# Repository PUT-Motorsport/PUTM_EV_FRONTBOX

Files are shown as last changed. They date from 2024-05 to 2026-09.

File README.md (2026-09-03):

# PUTM_EV_Frontbox

PCB board aquiring data from the front side of the vehicle.

# Features

- APPS
  - read position of acceleration pedal and send to VCU
  - two outputs: power (+5V) lines with separate regulators
  - two inputs: APPS signal lines
  - check plasubility between two signal lines
- Data acquisition
  - front and rear brake pressure measurement
  - safety sensing
  - brake pedal position sensor for regenerative braking

### APPS

- 2 linear potentiometers mounted on pedal
- hardware filter and voltage clamp
- 2 diffrent transfer function to detect implasubility when defect occurs

### Front and rear brake pressure

- two analog, 5V sensors
- hardware filter and voltage clamp

### Safety (shutdown circuit) sensing
Optocupler to check state of SDC curcuit, shift level from 24V to 3V3 and read on MCU digital input
The safety state will be measured at:
- left kill switch
- right kill switch
- driver's kill switch
- inertia switch
- BSPD
- brake overtravel
- suspension interlocks

### Brake pedal position sensor
TBD

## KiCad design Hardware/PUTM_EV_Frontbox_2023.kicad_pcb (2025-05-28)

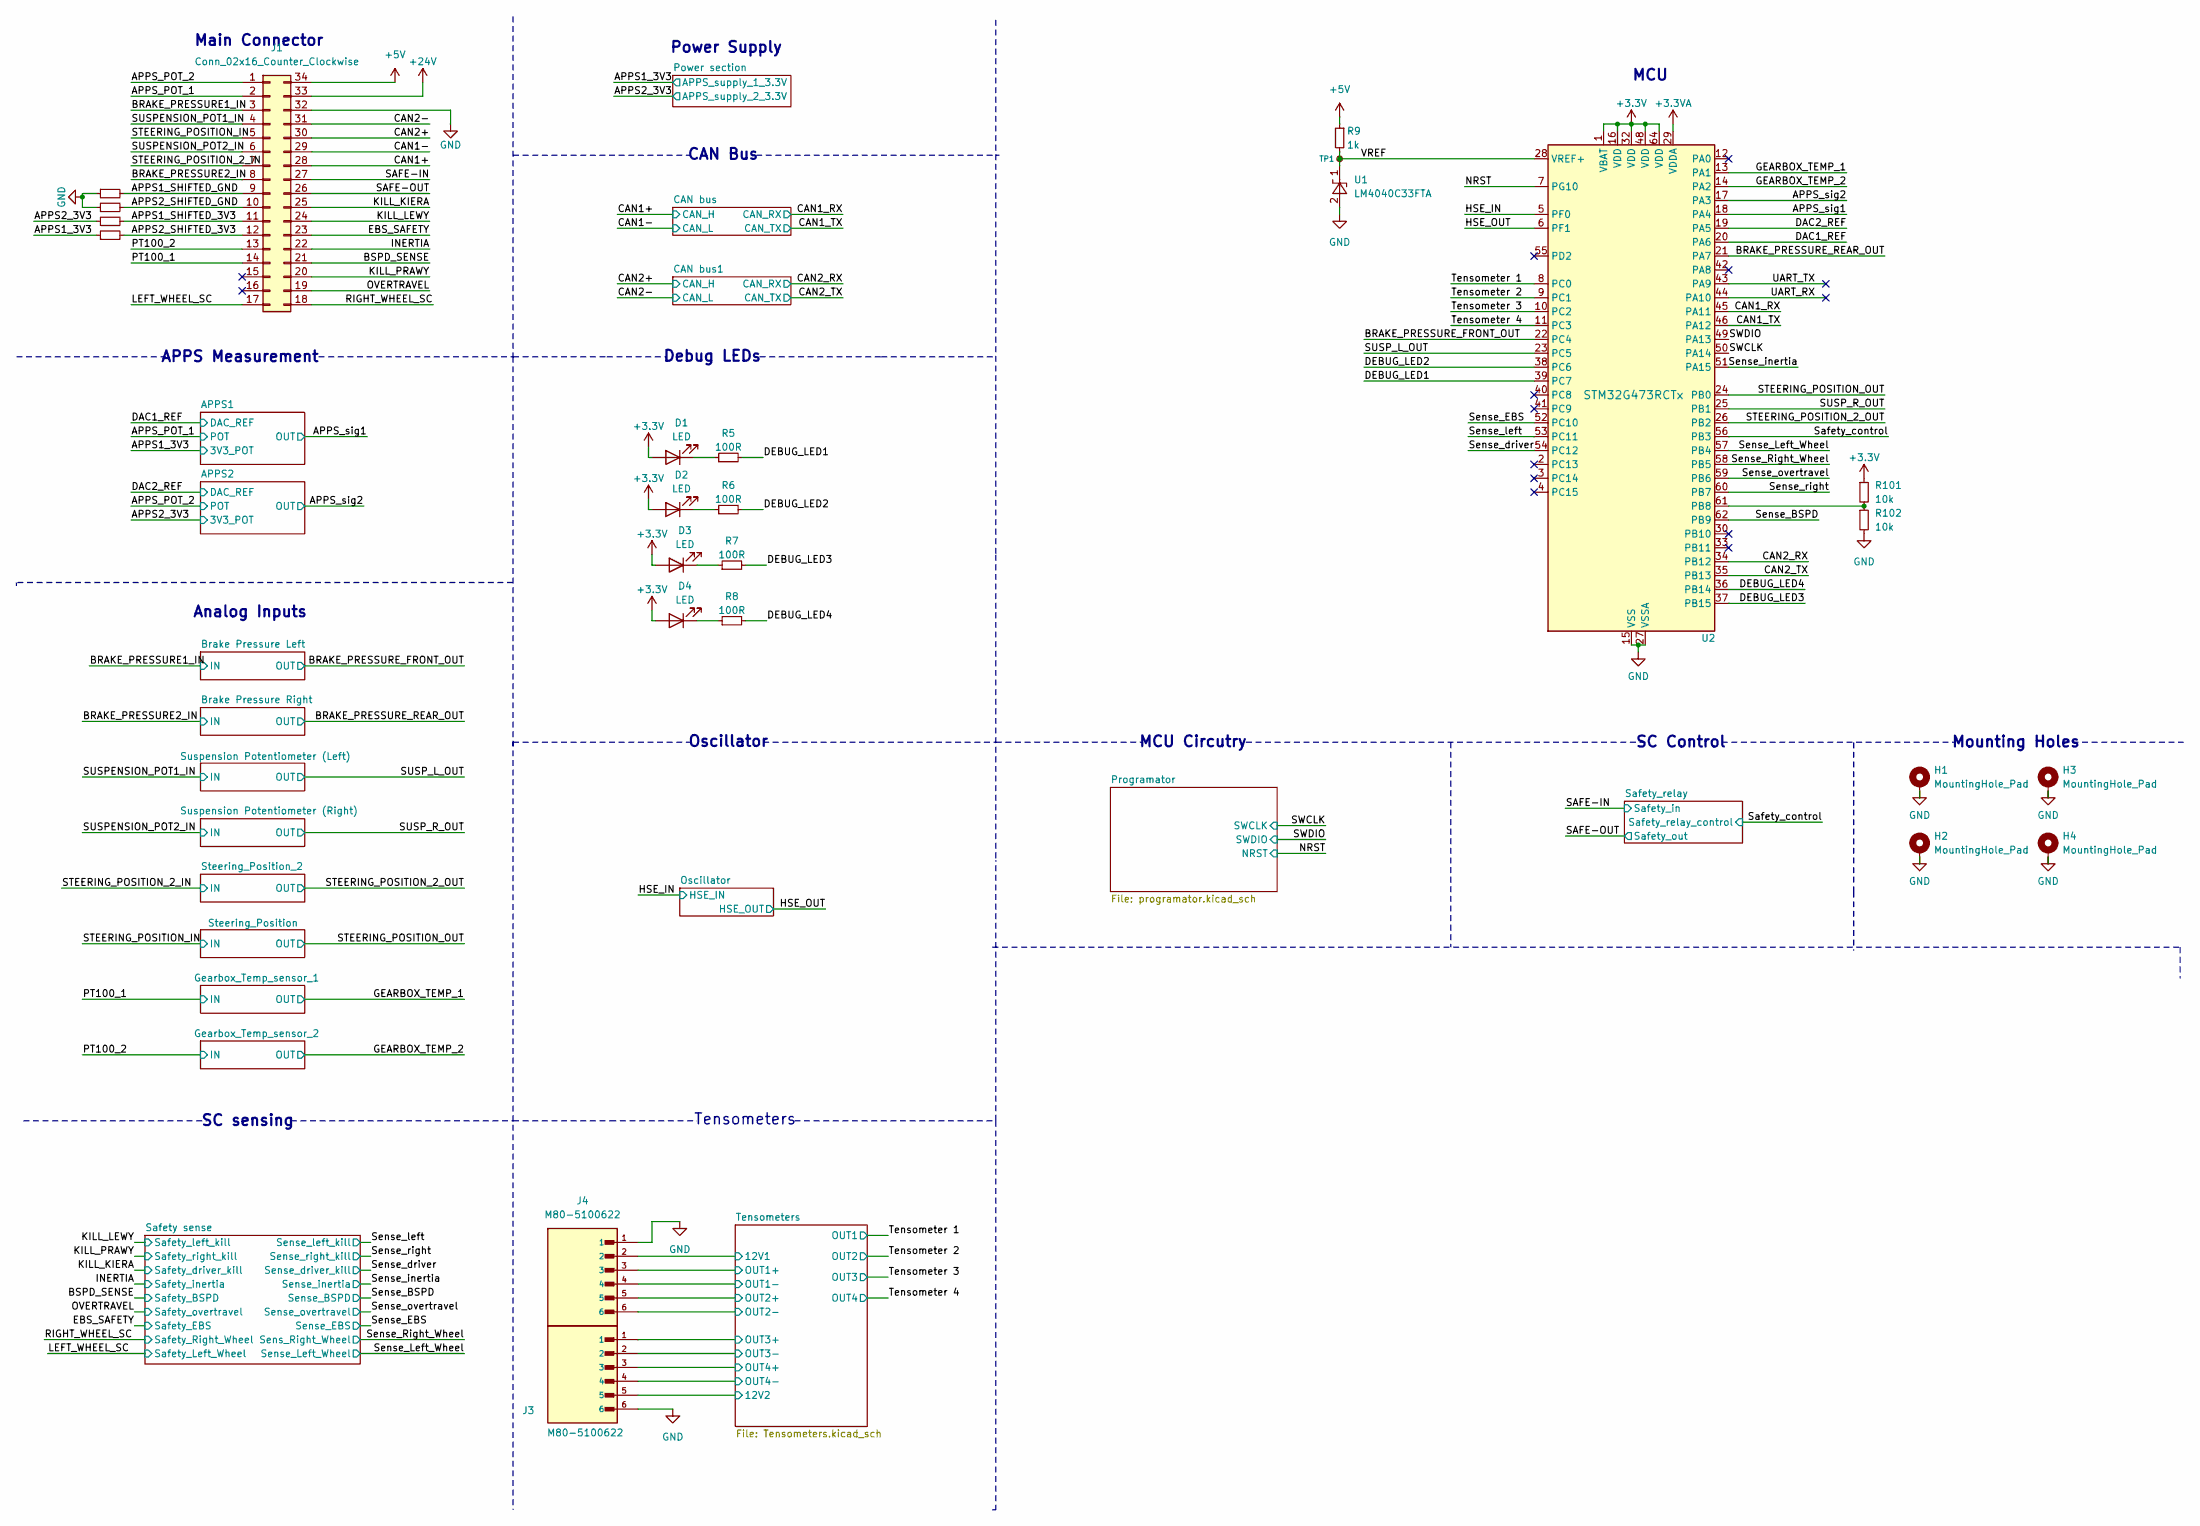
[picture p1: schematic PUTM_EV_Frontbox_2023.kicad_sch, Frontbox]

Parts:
D1, D2, D3, D4: LED; LED_0603_1608Metric_Pad1.05x0.95mm_HandSolder
H1, H2, H3, H4: MountingHole_Pad; MountingHole_3.2mm_M3_Pad_Via
J1: Conn_02x16_Counter_Clockwise; IDC-Header_2x17-1MP_P2.54mm_Latch6.5mm_Vertical
J3, J4: M80-5100622; M80-5100622_HARWIN_M80-5100622
R1, R2, R3, R4: 220R; R_0603_1608Metric_Pad0.98x0.95mm_HandSolder
R5, R6, R7, R8: 100R; R_0603_1608Metric_Pad0.98x0.95mm_HandSolder
R9: 1k; R_0603_1608Metric
R101, R102: 10k; R_0603_1608Metric
TP1: TestPoint_Small; TestPoint_THTPad_D1.0mm_Drill0.5mm
U1: LM4040C33FTA; SOT-23
U2: STM32G473RCTx; LQFP-64_10x10mm_P0.5mm

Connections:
+3.3V: D1.2 (A), D2.2 (A), D3.2 (A), D4.2 (A), R101.1, U2.1 (VBAT), U2.16 (VDD), U2.32 (VDD), U2.48 (VDD), U2.64 (VDD); also elsewhere on the board
+5V: J1.34, R9.1; also elsewhere on the board
+24V: J1.33; also elsewhere on the board
/APPS1_3V3: R4.1; also elsewhere on the board
/APPS1_SHIFTED_3V3: J1.11, R3.2
/APPS1_SHIFTED_GND: J1.9, R1.2
/APPS2_3V3: R3.1; also elsewhere on the board
/APPS2_SHIFTED_3V3: J1.12, R4.2
/APPS2_SHIFTED_GND: J1.10, R2.2
/APPS_POT_1: J1.2; also elsewhere on the board
/APPS_POT_2: J1.1; also elsewhere on the board
/BRAKE_PRESSURE1_IN: J1.3; also elsewhere on the board
/BRAKE_PRESSURE2_IN: J1.8; also elsewhere on the board
/BSPD_SENSE: J1.21; also elsewhere on the board
/CAN1+: J1.28; also elsewhere on the board
/CAN1-: J1.29; also elsewhere on the board
/CAN2+: J1.30; also elsewhere on the board
/CAN2-: J1.31; also elsewhere on the board
/DEBUG_LED1: R5.2, U2.39 (PC7); also elsewhere on the board
/DEBUG_LED2: R6.2, U2.38 (PC6); also elsewhere on the board
/DEBUG_LED3: R7.2, U2.37 (PB15); also elsewhere on the board
/DEBUG_LED4: R8.2, U2.36 (PB14); also elsewhere on the board
/EBS_SAFETY: J1.23; also elsewhere on the board
/INERTIA: J1.22; also elsewhere on the board
/KILL_KIERA: J1.25; also elsewhere on the board
/KILL_LEWY: J1.24; also elsewhere on the board
/KILL_PRAWY: J1.20; also elsewhere on the board
/LEFT_WHEEL_SC: J1.17; also elsewhere on the board
/OVERTRAVEL: J1.19; also elsewhere on the board
/PT100_1: J1.14; also elsewhere on the board
/PT100_2: J1.13; also elsewhere on the board
/RIGHT_WHEEL_SC: J1.18; also elsewhere on the board
/SAFE-IN: J1.27; also elsewhere on the board
/SAFE-OUT: J1.26; also elsewhere on the board
/STEERING_POSITION_2_IN: J1.7; also elsewhere on the board
/STEERING_POSITION_IN: J1.5; also elsewhere on the board
/SUSPENSION_POT1_IN: J1.4; also elsewhere on the board
/SUSPENSION_POT2_IN: J1.6; also elsewhere on the board
/Tensometers/12V1: J4.2; also elsewhere on the board
/Tensometers/12V2: J3.5; also elsewhere on the board
/Tensometers/OUT1+: J4.3; also elsewhere on the board
/Tensometers/OUT1-: J4.4; also elsewhere on the board
/Tensometers/OUT2+: J4.5; also elsewhere on the board
/Tensometers/OUT2-: J4.6; also elsewhere on the board
/Tensometers/OUT3+: J3.1; also elsewhere on the board
/Tensometers/OUT3-: J3.2; also elsewhere on the board
/Tensometers/OUT4+: J3.3; also elsewhere on the board
/Tensometers/OUT4-: J3.4; also elsewhere on the board
/VREF: R9.2, TP1.1, U1.1 (K), U2.28 (VREF+); also elsewhere on the board
GND: H1.1, H2.1, H3.1, H4.1, J1.32, J3.6, J4.1, R1.1, R2.1, R102.2, U1.2 (A), U2.15 (VSS), U2.27 (VSSA), U2.31 (VSS), U2.47 (VSS), U2.63 (VSS); also elsewhere on the board
unnamed: D1.1 (K), R5.1
unnamed: D2.1 (K), R6.1
unnamed: D3.1 (K), R7.1
unnamed: D4.1 (K), R8.1
unnamed 173: R101.2, R102.1, U2.61 (PB8); also elsewhere on the board

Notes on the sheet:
SC sensing
MCU Circutry
CAN Bus
Debug LEDs
Analog Inputs
Oscillator
Main Connector
Tensometers
MCU
SC Control
APPS Measurement
Power Supply
Mounting Holes

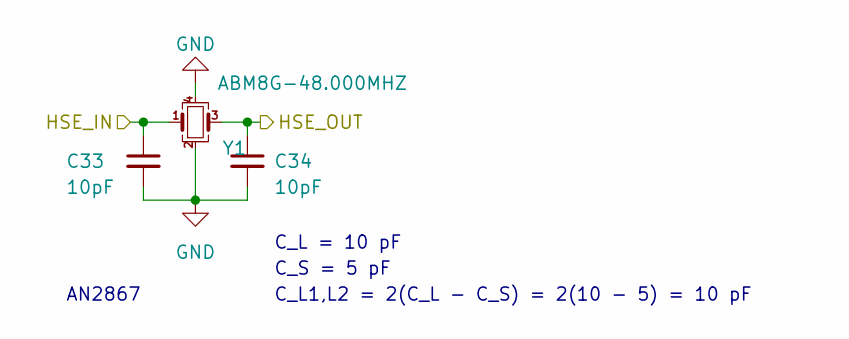
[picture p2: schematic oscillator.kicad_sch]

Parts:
C33, C34: 10pF; C_0402_1005Metric_Pad0.74x0.62mm_HandSolder
Y1: ABM8G-48.000MHZ; Crystal_SMD_Abracon_ABM8G-4Pin_3.2x2.5mm

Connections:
/HSE_IN: C33.1, Y1.1; also elsewhere on the board
/HSE_OUT: C34.1, Y1.3; also elsewhere on the board
GND: C33.2, C34.2, Y1.2, Y1.4; also elsewhere on the board

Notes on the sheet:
C_L = 10 pF
C_S = 5 pF
C_L1,L2 = 2(C_L - C_S) = 2(10 - 5) = 10 pF
AN2867

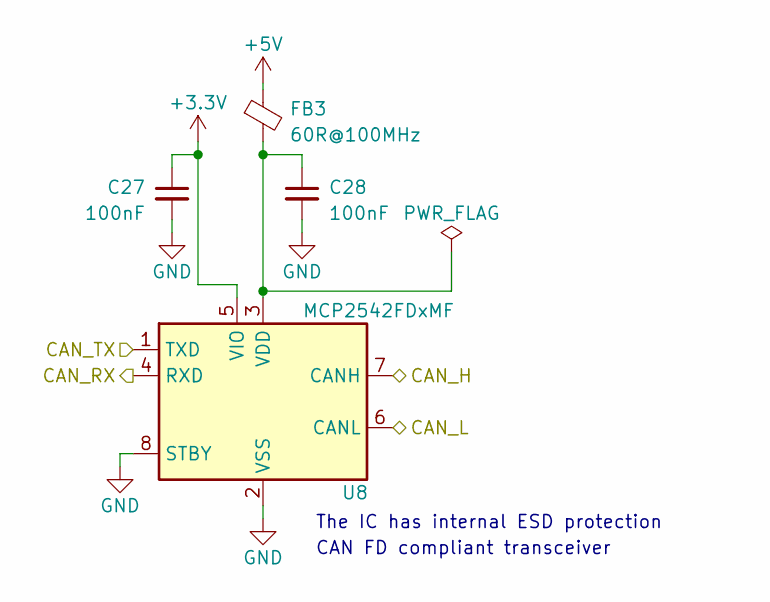
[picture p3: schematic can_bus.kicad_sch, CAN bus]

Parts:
C27, C28: 100nF; C_0402_1005Metric_Pad0.74x0.62mm_HandSolder
FB3: 60R@100MHz; L_0603_1608Metric
U8: MCP2542FDxMF; DFN-8-1EP_3x3mm_P0.65mm_EP1.55x2.4mm

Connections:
+3.3V: C27.1, U8.5 (VIO); also elsewhere on the board
+5V: FB3.1; also elsewhere on the board
/CAN1+: U8.7 (CANH); also elsewhere on the board
/CAN1-: U8.6 (CANL); also elsewhere on the board
/CAN1_RX: U8.4 (RXD); also elsewhere on the board
/CAN1_TX: U8.1 (TXD); also elsewhere on the board
GND: C27.2, C28.2, U8.2 (VSS), U8.8 (STBY), U8.9 (VSS); also elsewhere on the board
unnamed: C28.1, FB3.2, U8.3 (VDD)

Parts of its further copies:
C35, C36: 100nF; C_0402_1005Metric_Pad0.74x0.62mm_HandSolder
FB4: 60R@100MHz; L_0603_1608Metric
U14: MCP2542FDxMF; DFN-8-1EP_3x3mm_P0.65mm_EP1.55x2.4mm

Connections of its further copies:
+3.3V: C35.1, U14.5 (VIO); also elsewhere on the board
+5V: FB4.1; also elsewhere on the board
/CAN2+: U14.7 (CANH); also elsewhere on the board
/CAN2-: U14.6 (CANL); also elsewhere on the board
/CAN2_RX: U14.4 (RXD); also elsewhere on the board
/CAN2_TX: U14.1 (TXD); also elsewhere on the board
GND: C35.2, C36.2, U14.2 (VSS), U14.8 (STBY), U14.9 (VSS); also elsewhere on the board
unnamed: C36.1, FB4.2, U14.3 (VDD)

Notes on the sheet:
The IC has internal ESD protection
CAN FD compliant transceiver

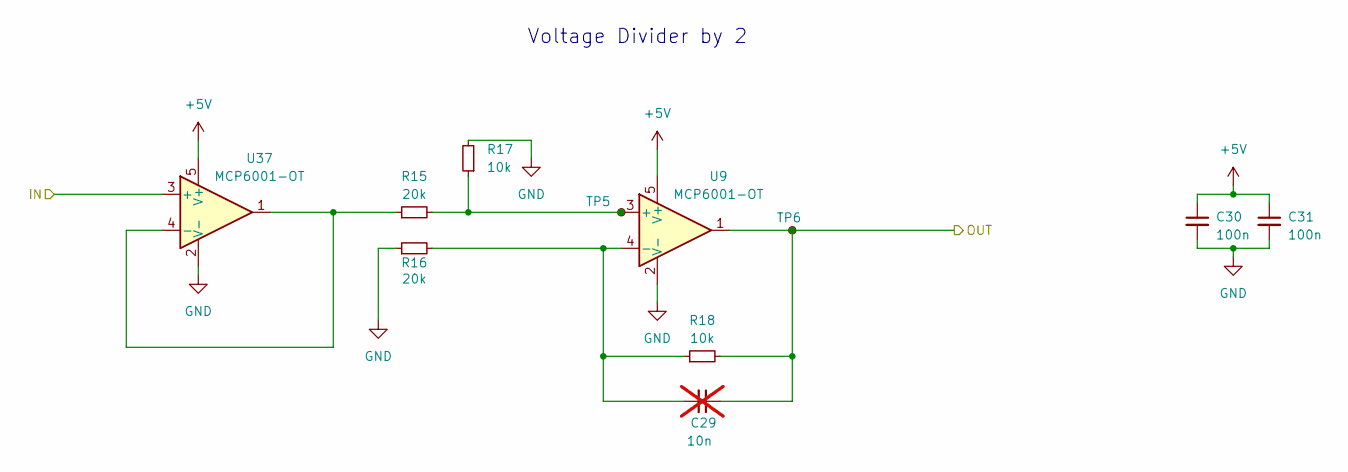
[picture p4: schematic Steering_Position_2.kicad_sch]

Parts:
C29: 10n; C_0603_1608Metric; not fitted
C30, C31: 100n; C_0603_1608Metric
R15, R16: 20k; R_0603_1608Metric
R17, R18: 10k; R_0603_1608Metric
TP5, TP6: TestPoint_Small; TestPoint_THTPad_D1.0mm_Drill0.5mm
U9, U37: MCP6001-OT; SOT-23-5

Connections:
+5V: C30.1, C31.1, U9.5 (V+), U37.5 (V+); also elsewhere on the board
/STEERING_POSITION_2_IN: U37.3 (+); also elsewhere on the board
/STEERING_POSITION_2_OUT: C29.1, R18.2, TP6.1, U9.1; also elsewhere on the board
GND: C30.2, C31.2, R16.1, R17.2, U9.2 (V-), U37.2 (V-); also elsewhere on the board
unnamed: R15.2, R17.1, TP5.1, U9.3 (+)
unnamed: C29.2, R16.2, R18.1, U9.4 (-)
unnamed: R15.1, U37.1, U37.4 (-)

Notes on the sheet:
Voltage Divider by 2

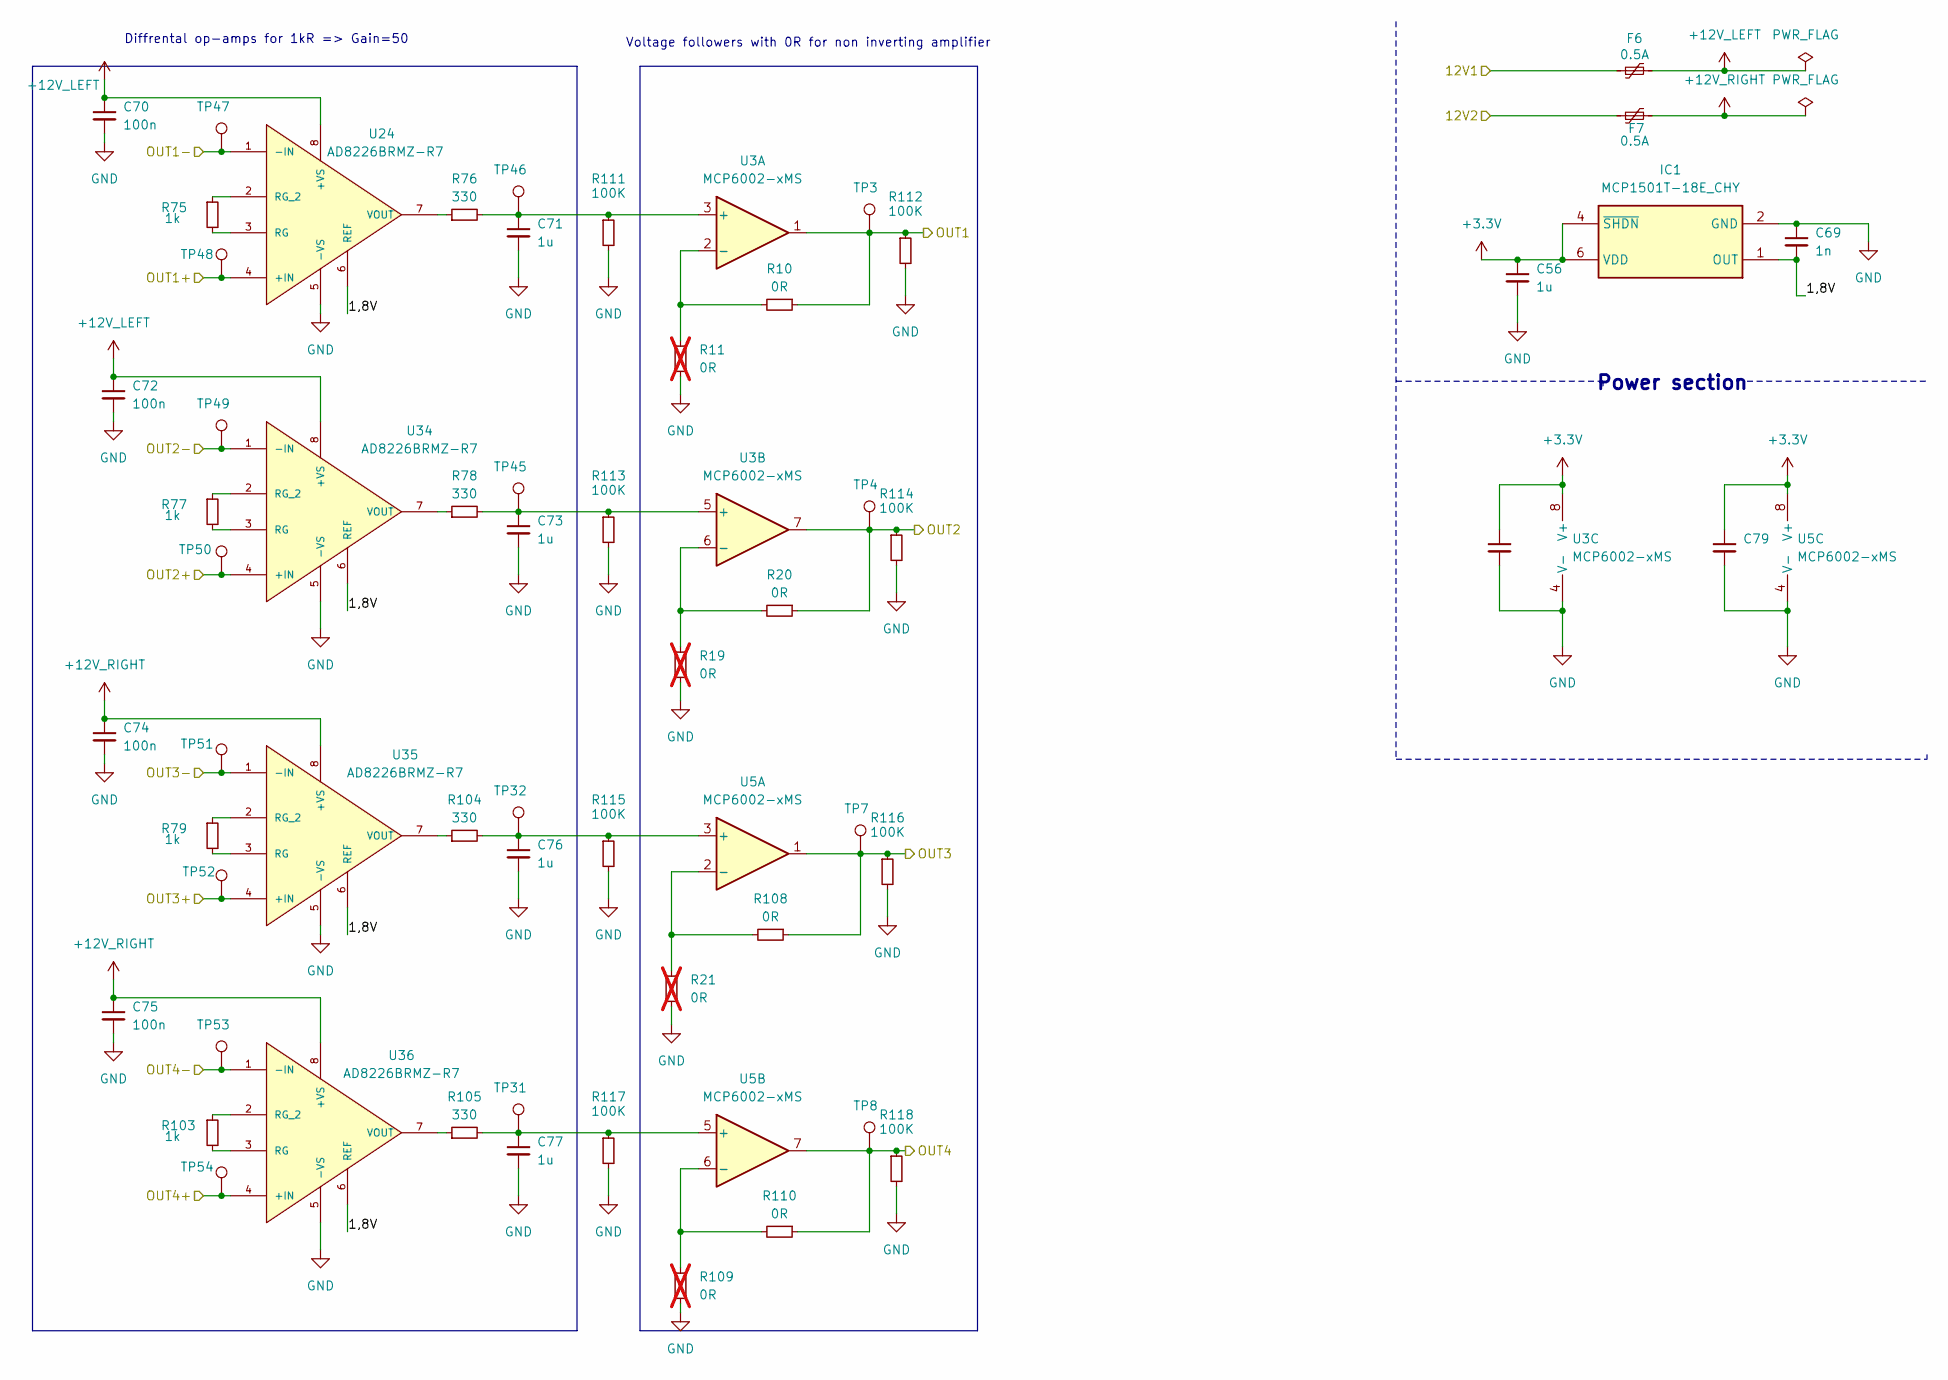
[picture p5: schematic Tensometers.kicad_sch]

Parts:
C56, C71, C73, C76, C77: 1u; C_0603_1608Metric
C69: 1n; C_0603_1608Metric
C70, C72, C74, C75, C78, C79: 100n; C_0603_1608Metric
F6, F7: 0.5A; Fuse_0805_2012Metric
IC1: MCP1501T-18E_CHY; SOT95P270X145-6N; Manufacturer_Part_Number MCP1501T-18E/CHY; Mouser Part Number 579-MCP1501T-18E/CHY
R10, R20, R108, R110: 0R; R_0603_1608Metric
R11, R19, R21, R109: 0R; R_0603_1608Metric; not fitted
R75, R77, R79, R103: 1k; R_0603_1608Metric
R76, R78, R104, R105: 330; R_0603_1608Metric
R111, R112, R113, R114, R115, R116, R117, R118: 100K; R_0603_1608Metric
TP3, TP4, TP7, TP8, TP31, TP32, TP45, TP46, TP47, TP48, TP49, TP50, TP51, TP52, TP53, TP54: BR_N; TestPoint_THTPad_D1.0mm_Drill0.5mm
U3, U5: MCP6002-xMS; SOP65P490X110-8N
U24, U34, U35, U36: AD8226BRMZ-R7; AD8226BRMZ-R7_SOP65P490X110-8N; MPN AD8226BRMZ-R7

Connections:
+3.3V: C56.1, C78.1, C79.1, IC1.4 (~SHDN), IC1.6 (VDD), U3.8 (V+), U5.8 (V+); also elsewhere on the board
+12V_LEFT: C70.1, C72.1, F6.2, U24.8 (+VS), U34.8 (+VS)
+12V_RIGHT: C74.1, C75.1, F7.2, U35.8 (+VS), U36.8 (+VS)
/Tensometer 1: R10.1, R112.1, TP3.1, U3.1; also elsewhere on the board
/Tensometer 2: R20.1, R114.1, TP4.1, U3.7; also elsewhere on the board
/Tensometer 3: R108.1, R116.1, TP7.1, U5.1; also elsewhere on the board
/Tensometer 4: R110.1, R118.1, TP8.1, U5.7; also elsewhere on the board
/Tensometers/1,8V: C69.2, IC1.1 (OUT), U24.6 (REF), U34.6 (REF), U35.6 (REF), U36.6 (REF)
/Tensometers/12V1: F6.1; also elsewhere on the board
/Tensometers/12V2: F7.1; also elsewhere on the board
/Tensometers/OUT1+: TP48.1, U24.4 (+IN); also elsewhere on the board
/Tensometers/OUT1-: TP47.1, U24.1 (-IN); also elsewhere on the board
/Tensometers/OUT2+: TP50.1, U34.4 (+IN); also elsewhere on the board
/Tensometers/OUT2-: TP49.1, U34.1 (-IN); also elsewhere on the board
/Tensometers/OUT3+: TP52.1, U35.4 (+IN); also elsewhere on the board
/Tensometers/OUT3-: TP51.1, U35.1 (-IN); also elsewhere on the board
/Tensometers/OUT4+: TP54.1, U36.4 (+IN); also elsewhere on the board
/Tensometers/OUT4-: TP53.1, U36.1 (-IN); also elsewhere on the board
GND: C56.2, C69.1, C70.2, C71.2, C72.2, C73.2, C74.2, C75.2, C76.2, C77.2, C78.2, C79.2, IC1.2 (GND), IC1.3 (GND_2), IC1.5 (GND_3), R11.2, R19.2, R21.2, R109.2, R111.2, R112.2, R113.2, R114.2, R115.2, R116.2, R117.2, R118.2, U3.4 (V-), U5.4 (V-), U24.5 (-VS), U34.5 (-VS), U35.5 (-VS), U36.5 (-VS); also elsewhere on the board
unnamed: C71.1, R76.2, R111.1, TP46.1, U3.3 (+)
unnamed: R10.2, R11.1, U3.2 (-)
unnamed: C73.1, R78.2, R113.1, TP45.1, U3.5 (+)
unnamed: R19.1, R20.2, U3.6 (-)
unnamed: C76.1, R104.2, R115.1, TP32.1, U5.3 (+)
unnamed: R21.1, R108.2, U5.2 (-)
unnamed: C77.1, R105.2, R117.1, TP31.1, U5.5 (+)
unnamed: R109.1, R110.2, U5.6 (-)
unnamed: R75.2, U24.3 (RG)
unnamed: R75.1, U24.2 (RG_2)
unnamed: R76.1, U24.7 (VOUT)
unnamed: R77.2, U34.3 (RG)
unnamed: R77.1, U34.2 (RG_2)
unnamed: R78.1, U34.7 (VOUT)
unnamed: R79.2, U35.3 (RG)
unnamed: R79.1, U35.2 (RG_2)
unnamed: R104.1, U35.7 (VOUT)
unnamed: R103.2, U36.3 (RG)
unnamed: R103.1, U36.2 (RG_2)
unnamed: R105.1, U36.7 (VOUT)

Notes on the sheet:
Power section
Voltage followers with 0R for non inverting amplifier
Diffrental op-amps for 1kR => Gain=50

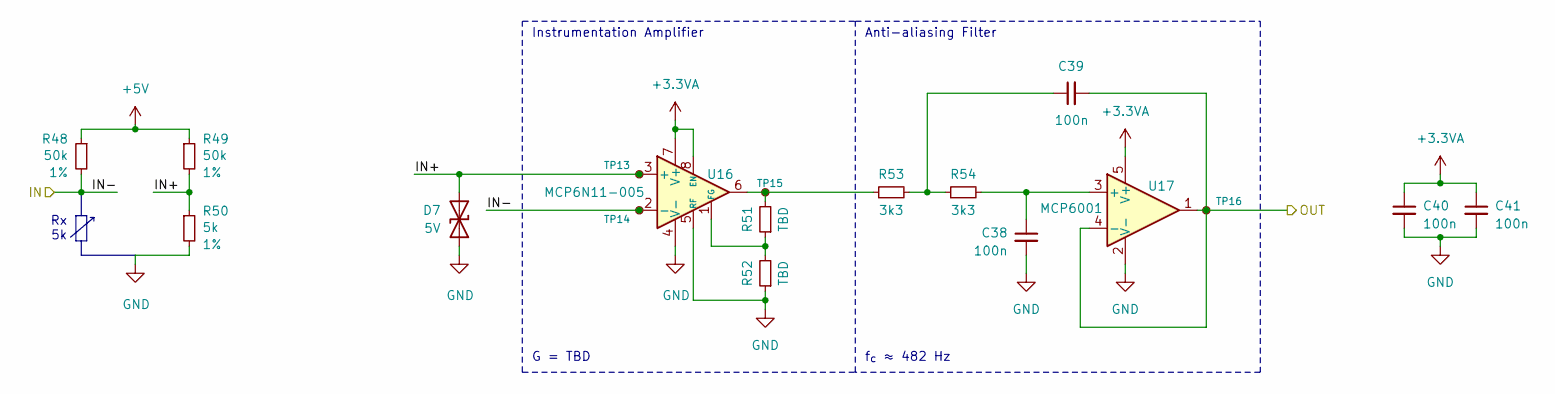
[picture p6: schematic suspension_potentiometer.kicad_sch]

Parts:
C38, C39, C40: 100n; C_0603_1608Metric
C41: 100n; C_0402_1005Metric_Pad0.74x0.62mm_HandSolder
D7: 5V; D_SOD-523
R48, R49: 50k; R_0603_1608Metric; Tolerance 1%
R50: 5k; R_0603_1608Metric; Tolerance 1%
R51, R52: TBD; R_0603_1608Metric
R53, R54: 3k3; R_0603_1608Metric
TP13, TP14, TP15, TP16: TestPoint_Small; TestPoint_THTPad_D1.0mm_Drill0.5mm
U16: MCP6N11-005; TDFN-8-1EP_3x2mm_P0.5mm_EP1.70x1.65mm
U17: MCP6001; SOT-23-5

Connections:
+3.3VA: C40.1, C41.1, U16.7 (V+), U16.8 (EN), U17.5 (V+); also elsewhere on the board
+5V: R48.1, R49.1; also elsewhere on the board
/SUSPENSION_POT1_IN: R48.2, TP14.1, U16.2 (-); also elsewhere on the board
/SUSP_L_OUT: C39.2, TP16.1, U17.1, U17.4 (-); also elsewhere on the board
/Suspension Potentiometer (Left)/IN+: D7.2 (A2), R49.2, R50.1, TP13.1, U16.3 (+)
GND: C38.2, C40.2, C41.2, D7.1 (A1), R50.2, R52.1, U16.4 (V-), U16.5 (RF), U16.9 (EP), U17.2 (V-); also elsewhere on the board
unnamed: C39.1, R53.2, R54.1
unnamed: R51.2, R53.1, TP15.1, U16.6
unnamed: R51.1, R52.2, U16.1 (FG)
unnamed: C38.1, R54.2, U17.3 (+)

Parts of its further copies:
C57, C58, C59, C61, C62, C63, C65, C66, C67: 100n; C_0603_1608Metric
C60, C64, C68: 100n; C_0402_1005Metric_Pad0.74x0.62mm_HandSolder
D11, D12, D13: 5V; D_SOD-523
R80, R81, R87, R88, R94, R95: 50k; R_0603_1608Metric; Tolerance 1%
R82, R89, R96: 5k; R_0603_1608Metric; Tolerance 1%
R83, R84, R90, R91, R97, R98: TBD; R_0603_1608Metric
R85, R86, R92, R93, R99, R100: 3k3; R_0603_1608Metric
TP33, TP34, TP35, TP36, TP37, TP38, TP39, TP40, TP41, TP42, TP43, TP44: TestPoint_Small; TestPoint_THTPad_D1.0mm_Drill0.5mm
U25, U27, U29: MCP6N11-005; TDFN-8-1EP_3x2mm_P0.5mm_EP1.70x1.65mm
U26, U28, U30: MCP6001; SOT-23-5

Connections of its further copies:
+3.3VA: C59.1, C60.1, C63.1, C64.1, C67.1, C68.1, U25.7 (V+), U25.8 (EN), U26.5 (V+), U27.7 (V+), U27.8 (EN), U28.5 (V+), U29.7 (V+), U29.8 (EN), U30.5 (V+); also elsewhere on the board
+5V: R80.1, R81.1, R87.1, R88.1, R94.1, R95.1; also elsewhere on the board
/GEARBOX_TEMP_1: C62.2, TP40.1, U28.1, U28.4 (-); also elsewhere on the board
/GEARBOX_TEMP_2: C66.2, TP44.1, U30.1, U30.4 (-); also elsewhere on the board
/Gearbox_Temp_sensor_1/IN+: D12.2 (A2), R88.2, R89.1, TP37.1, U27.3 (+)
/Gearbox_Temp_sensor_2/IN+: D13.2 (A2), R95.2, R96.1, TP41.1, U29.3 (+)
/PT100_1: R87.2, TP38.1, U27.2 (-); also elsewhere on the board
/PT100_2: R94.2, TP42.1, U29.2 (-); also elsewhere on the board
/SUSPENSION_POT2_IN: R80.2, TP34.1, U25.2 (-); also elsewhere on the board
/SUSP_R_OUT: C58.2, TP36.1, U26.1, U26.4 (-); also elsewhere on the board
/Suspension Potentiometer (Right)/IN+: D11.2 (A2), R81.2, R82.1, TP33.1, U25.3 (+)
GND: C57.2, C59.2, C60.2, C61.2, C63.2, C64.2, C65.2, C67.2, C68.2, D11.1 (A1), D12.1 (A1), D13.1 (A1), R82.2, R84.1, R89.2, R91.1, R96.2, R98.1, U25.4 (V-), U25.5 (RF), U25.9 (EP), U26.2 (V-), U27.4 (V-), U27.5 (RF), U27.9 (EP), U28.2 (V-), U29.4 (V-), U29.5 (RF), U29.9 (EP), U30.2 (V-); also elsewhere on the board
unnamed: C58.1, R85.2, R86.1
unnamed: C62.1, R92.2, R93.1
unnamed: C66.1, R99.2, R100.1
unnamed: R83.2, R85.1, TP35.1, U25.6
unnamed: R90.2, R92.1, TP39.1, U27.6
unnamed: R97.2, R99.1, TP43.1, U29.6
unnamed: R83.1, R84.2, U25.1 (FG)
unnamed: C57.1, R86.2, U26.3 (+)
unnamed: R90.1, R91.2, U27.1 (FG)
unnamed: C61.1, R93.2, U28.3 (+)
unnamed: R97.1, R98.2, U29.1 (FG)
unnamed: C65.1, R100.2, U30.3 (+)

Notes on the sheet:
G = TBD
f_{c} ≈ 482 Hz
Instrumentation Amplifier
Rx 5k
Anti-aliasing Filter

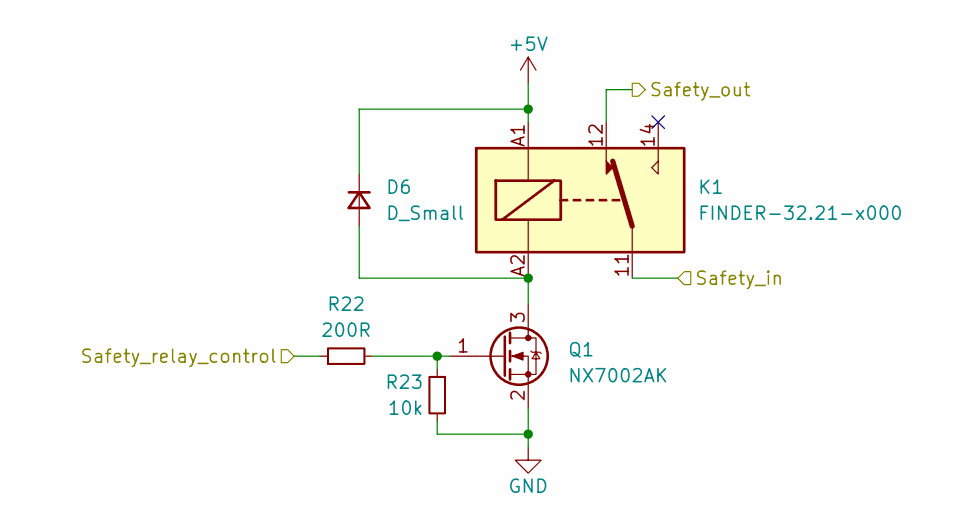
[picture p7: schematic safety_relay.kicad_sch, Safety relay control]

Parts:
D6: D_Small; D_0805_2012Metric_Pad1.15x1.40mm_HandSolder
K1: FINDER-32.21-x000; Relay_SPDT_Finder_32.21-x000
Q1: NX7002AK; SOT-23
R22: 200R; R_0402_1005Metric
R23: 10k; R_0402_1005Metric

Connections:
+5V: D6.1 (K), K1.A1; also elsewhere on the board
/SAFE-IN: K1.11; also elsewhere on the board
/SAFE-OUT: K1.12; also elsewhere on the board
/Safety_control: R22.1; also elsewhere on the board
GND: Q1.2 (S), R23.2; also elsewhere on the board
unnamed: D6.2 (A), K1.A2, Q1.3 (D)
unnamed: Q1.1 (G), R22.2, R23.1

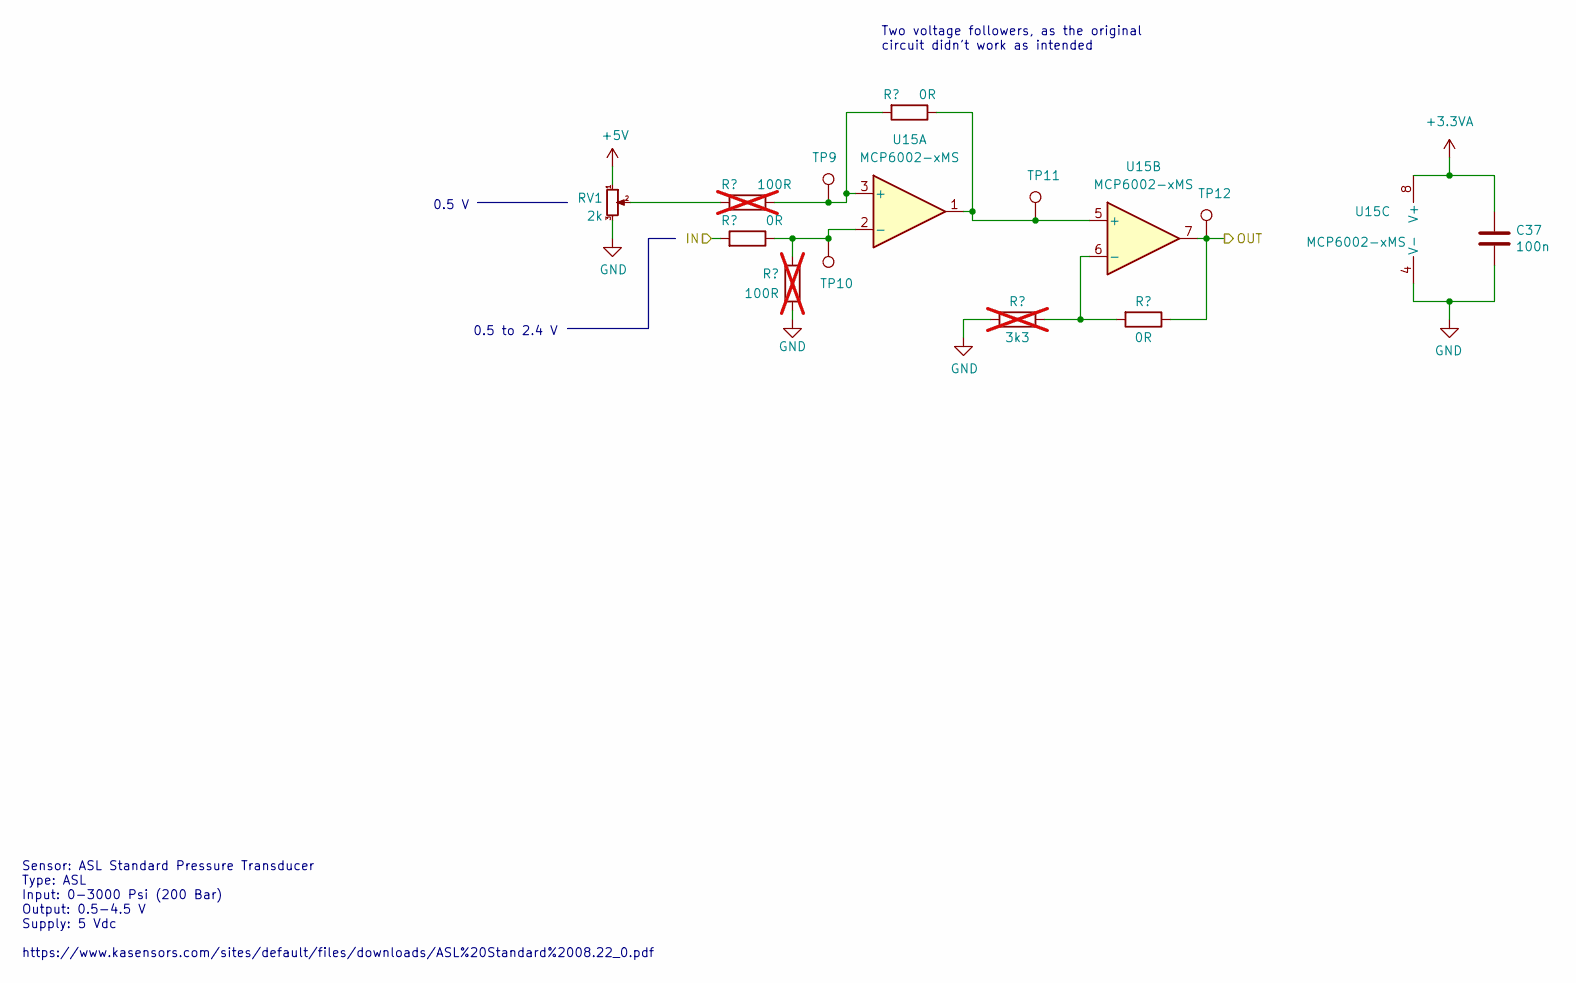
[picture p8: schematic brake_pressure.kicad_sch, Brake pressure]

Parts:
C37: 100n; C_0603_1608Metric_Pad1.08x0.95mm_HandSolder
R42, R44: 100R; R_0603_1608Metric_Pad0.98x0.95mm_HandSolder; not fitted
R43, R45, R47: 0R; R_0603_1608Metric_Pad0.98x0.95mm_HandSolder
R46: 3k3; R_0603_1608Metric_Pad0.98x0.95mm_HandSolder; not fitted
RV1: 2k; Potentiometer_Bourns_3214J_Horizontal
TP9: BR_N; TestPoint_THTPad_D1.0mm_Drill0.5mm
TP10: BR_P; TestPoint_THTPad_D1.0mm_Drill0.5mm
TP11: BR_MID; TestPoint_THTPad_D1.0mm_Drill0.5mm
TP12: BR_OUT; TestPoint_THTPad_D1.0mm_Drill0.5mm
U15: MCP6002-xMS; SOP65P490X110-8N

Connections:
+3.3VA: C37.1, U15.8 (V+); also elsewhere on the board
+5V: RV1.1; also elsewhere on the board
/BRAKE_PRESSURE1_IN: R43.2; also elsewhere on the board
/BRAKE_PRESSURE_FRONT_OUT: R47.1, TP12.1, U15.7; also elsewhere on the board
GND: C37.2, R44.1, R46.2, RV1.3, U15.4 (V-); also elsewhere on the board
unnamed: R42.2, RV1.2
unnamed: R42.1, R45.2, TP9.1, U15.3 (+)
unnamed: R43.1, R44.2, TP10.1, U15.2 (-)
unnamed: R45.1, TP11.1, U15.1, U15.5 (+)
unnamed: R46.1, R47.2, U15.6 (-)

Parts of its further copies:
C42: 100n; C_0603_1608Metric_Pad1.08x0.95mm_HandSolder
R55, R57: 100R; R_0603_1608Metric_Pad0.98x0.95mm_HandSolder; not fitted
R56, R58, R60: 0R; R_0603_1608Metric_Pad0.98x0.95mm_HandSolder
R59: 3k3; R_0603_1608Metric_Pad0.98x0.95mm_HandSolder; not fitted
RV2: 2k; Potentiometer_Bourns_3214J_Horizontal
TP17: BR_N; TestPoint_THTPad_D1.0mm_Drill0.5mm
TP18: BR_P; TestPoint_THTPad_D1.0mm_Drill0.5mm
TP19: BR_MID; TestPoint_THTPad_D1.0mm_Drill0.5mm
TP20: BR_OUT; TestPoint_THTPad_D1.0mm_Drill0.5mm
U18: MCP6002-xMS; SOP65P490X110-8N

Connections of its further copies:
+3.3VA: C42.1, U18.8 (V+); also elsewhere on the board
+5V: RV2.1; also elsewhere on the board
/BRAKE_PRESSURE2_IN: R56.2; also elsewhere on the board
/BRAKE_PRESSURE_REAR_OUT: R60.1, TP20.1, U18.7; also elsewhere on the board
GND: C42.2, R57.1, R59.2, RV2.3, U18.4 (V-); also elsewhere on the board
unnamed: R55.2, RV2.2
unnamed: R55.1, R58.2, TP17.1, U18.3 (+)
unnamed: R56.1, R57.2, TP18.1, U18.2 (-)
unnamed: R58.1, TP19.1, U18.1, U18.5 (+)
unnamed: R59.1, R60.2, U18.6 (-)

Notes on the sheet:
Sensor: ASL Standard Pressure Transducer Type: ASL Input: 0-3000 Psi (200 Bar) Output: 0.5-4.5 V Supply: 5 Vdc https://www.kasensors.com/sites/default/files/downloads/ASL%20Standard%2008.22_0.pdf
Two voltage followers, as the original circuit didn't work as intended
0.5 to 2.4 V
0.5 V

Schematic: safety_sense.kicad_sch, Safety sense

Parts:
R24, R25, R26, R27, R28, R34, R35, R36, R37: 2k; R_0402_1005Metric
R29, R30, R31, R32, R33, R38, R39, R40, R41: 10k; R_0402_1005Metric
U11: FODM217B; SOP-4_4.4x2.6mm_P1.27mm
U12, U13: TLP291-4; SOIC-16_4.55x10.3mm_P1.27mm

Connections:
+3.3V: R29.1, R30.1, R31.1, R32.1, R33.1, R38.1, R39.1, R40.1, R41.1; also elsewhere on the board
/BSPD_SENSE: R25.1; also elsewhere on the board
/EBS_SAFETY: R36.1; also elsewhere on the board
/INERTIA: R37.1; also elsewhere on the board
/KILL_KIERA: R34.1; also elsewhere on the board
/KILL_LEWY: R35.1; also elsewhere on the board
/KILL_PRAWY: R26.1; also elsewhere on the board
/LEFT_WHEEL_SC: R24.1; also elsewhere on the board
/OVERTRAVEL: R27.1; also elsewhere on the board
/RIGHT_WHEEL_SC: R28.1; also elsewhere on the board
/Safety sense/SLW_A: R24.2, U11.1
/Sense_BSPD: R30.2, U12.16; also elsewhere on the board
/Sense_EBS: R40.2, U13.12; also elsewhere on the board
/Sense_Left_Wheel: R29.2, U11.4; also elsewhere on the board
/Sense_Right_Wheel: R33.2, U12.10; also elsewhere on the board
/Sense_driver: R38.2, U13.16; also elsewhere on the board
/Sense_inertia: R41.2, U13.10; also elsewhere on the board
/Sense_left: R39.2, U13.14; also elsewhere on the board
/Sense_overtravel: R32.2, U12.12; also elsewhere on the board
/Sense_right: R31.2, U12.14; also elsewhere on the board
GND: U11.2, U11.3, U12.2, U12.4, U12.6, U12.8, U12.9, U12.11, U12.13, U12.15, U13.2, U13.4, U13.6, U13.8, U13.9, U13.11, U13.13, U13.15; also elsewhere on the board
unnamed: R25.2, U12.1
unnamed: R26.2, U12.3
unnamed: R27.2, U12.5
unnamed: R28.2, U12.7
unnamed: R34.2, U13.1
unnamed: R35.2, U13.3
unnamed: R36.2, U13.5
unnamed: R37.2, U13.7

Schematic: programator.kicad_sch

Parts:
F5: Fuse_Small; Fuse_0805_2012Metric
U32: STLINK-V3MODS; MODULE_STLINK-V3MODS; PARTREV 1; DigiKey_Part_Number 497-STLINK-V3MODS-ND

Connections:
+5V: F5.1; also elsewhere on the board
/NRST: U32.31 (T_NRST); also elsewhere on the board
/SWCLK: U32.13 (T_JCLK/T_SWCLK); also elsewhere on the board
/SWDIO: U32.4 (T_JTMS/T_SWDIO); also elsewhere on the board
GND: U32.5 (GNDDETECT), U32.8 (GND_2), U32.24 (GND), U32.26 (GND2), U32.27 (GND3), U32.29 (GND4); also elsewhere on the board
unnamed: F5.2, U32.22 (5V_OPT)

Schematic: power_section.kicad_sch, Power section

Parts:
C3, C5: 2u2; C_0805_2012Metric; Rated Voltage 35V
C4, C6, C9, C23, C24, C25, C26: 1uF; C_0402_1005Metric_Pad0.74x0.62mm_HandSolder
C7, C8: 4u7; C_0805_2012Metric; Rated Voltage 35V
C10, C11, C18, C20: 22uF; C_0805_2012Metric; Manufacturer_Part_Number CL21A107MQYNNWE; Mouser Part Number 810-C2012X5R1V226MAC
C12, C13, C14, C17, C19, C21: 100nF; C_0402_1005Metric_Pad0.74x0.62mm_HandSolder
C15, C16: 100nF; C_0603_1608Metric; Manufacturer_Part_Number C0603C104J3RACTU; Mouser Part Number --
F1, F4: 1.5A; Fuse_1812_4532Metric
F2, F3: 300mA; Fuse_0603_1608Metric_Pad1.05x0.95mm_HandSolder
FB2: 1000Ω@100MHz; L_0603_1608Metric
IC2: TPS54202HDDCR; SOT-23-6; Mouser Part Number 595-TPS54202HDDCR
L1: 1u5; L_Abracon_ASPI-4030S
L2: 68uH/1.4A; L_TDK_VLS6045EX_VLS6045AF; Mouser Part Number 810-VLS6045EX-680M
R12: 510k; R_0603_1608Metric; Manufacturer_Part_Number RT0603DRD07510KL; Mouser Part Number 603-RT0603DRD07510KL
R13: 13.3k; R_0603_1608Metric; Manufacturer_Part_Number RT0603DRE0713K3L; Mouser Part Number 603-RT0603DRE0713K3L
R14: 100k; R_0603_1608Metric; Manufacturer_Part_Number RT0603DRE07100KL; Mouser Part Number --
R119: 43k; R_0603_1608Metric; Manufacturer_Part_Number RT0603DRD07510KL; Mouser Part Number 603-RT0603DRD07510KL
TP2: TestPoint_Small; TestPoint_THTPad_D1.0mm_Drill0.5mm
U4, U6, U7: TLV743P; SOT-23-5_HandSoldering

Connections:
+3.3V: C6.1, C13.1, C14.1, C17.1, C19.1, C21.1, FB2.1, U4.5 (OUT); also elsewhere on the board
+3.3VA: C9.1, C12.1, FB2.2; also elsewhere on the board
+5V: C4.1, C23.1, C24.1, F2.1, F3.1, F4.2, U4.1 (IN), U4.3 (EN); also elsewhere on the board
+24V: F1.1; also elsewhere on the board
/APPS1_3V3: C25.1, U6.5 (OUT); also elsewhere on the board
/APPS2_3V3: C26.1, U7.5 (OUT); also elsewhere on the board
/Power section/5V_UNFUSED: C18.1, C20.1, F4.1, L2.2, R14.2
/Power section/+24V_FUSED: C3.1, C5.1, F1.2, L1.1
/Power section/BOOT_5V: C16.1, IC2.6 (BOOT)
/Power section/EN_5V: IC2.5 (EN), R12.1, R119.1
/Power section/FB_5V: IC2.4 (FB), R13.2, R14.1
/Power section/SW_5V: C16.2, IC2.2 (SW), L2.1
GND: C3.2, C4.2, C5.2, C6.2, C7.2, C8.2, C9.2, C10.1, C11.1, C12.2, C13.2, C14.2, C15.1, C17.2, C18.2, C19.2, C20.2, C21.2, C23.2, C24.2, C25.2, C26.2, IC2.1 (GND), R13.1, R119.2, U4.2 (GND), U6.2 (GND), U7.2 (GND); also elsewhere on the board
unnamed: C7.1, C8.1, C10.2, C11.2, C15.2, IC2.3 (VIN), L1.2, R12.2, TP2.1
unnamed: F2.2, U6.1 (IN), U6.3 (EN)
unnamed: F3.2, U7.1 (IN), U7.3 (EN)

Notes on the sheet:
APPS Potentiometer 2 supply
5V Power supply
Decoupling capacitors
3V3
AN5093 Sect. 7.4 and 2.1.3
This resistor ensures that APPS's potentiometers have non intersecting transfer functions. The other potentiometer has an identical resistor on the negative side.
APPS Potentiometer 1 supply
MCU supply

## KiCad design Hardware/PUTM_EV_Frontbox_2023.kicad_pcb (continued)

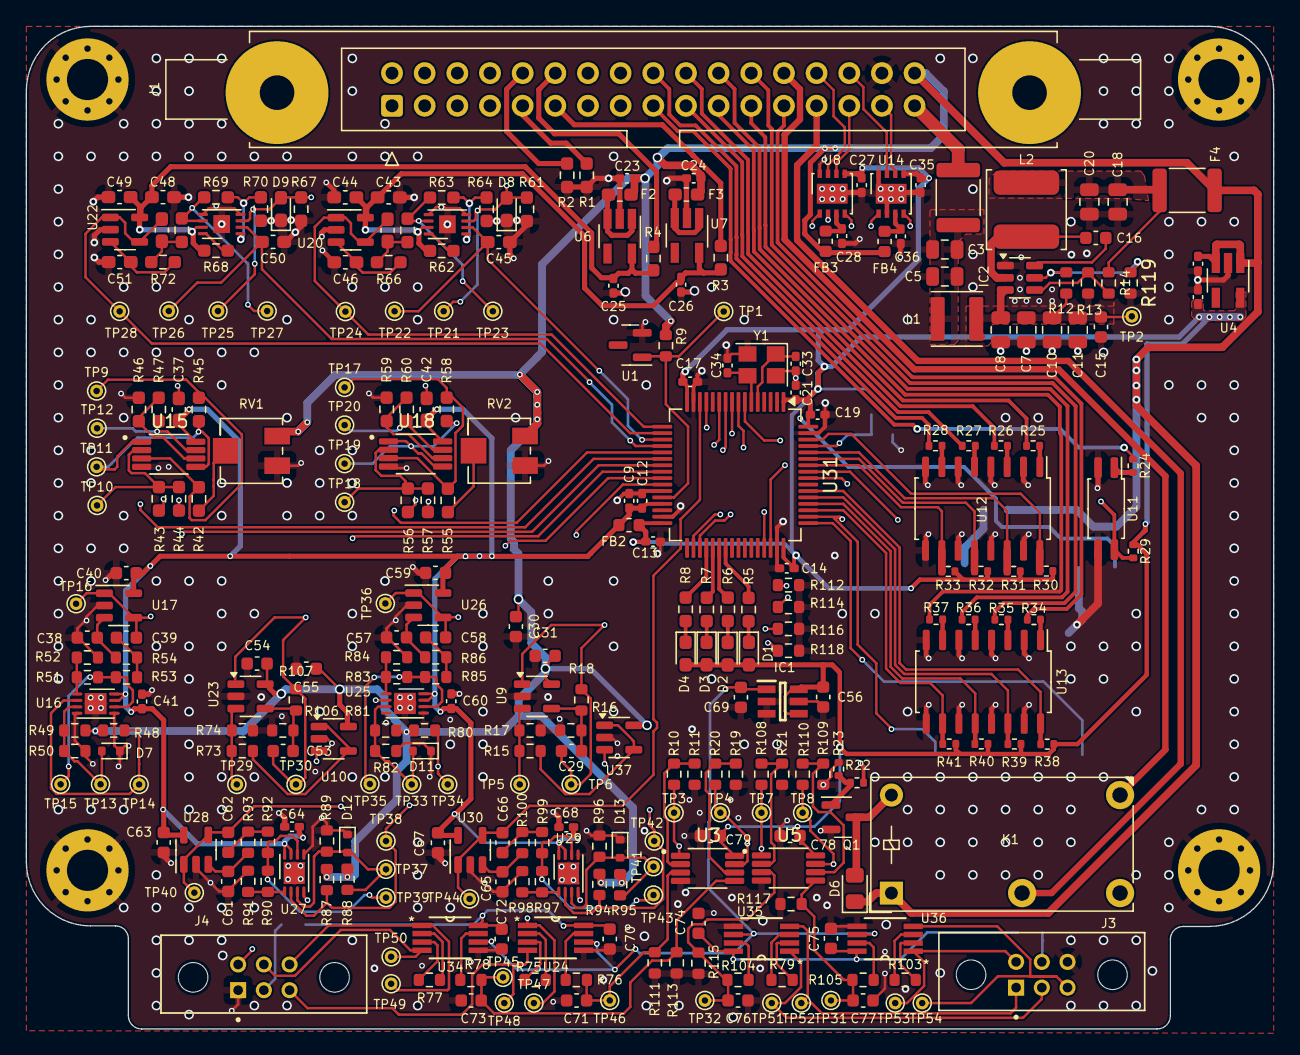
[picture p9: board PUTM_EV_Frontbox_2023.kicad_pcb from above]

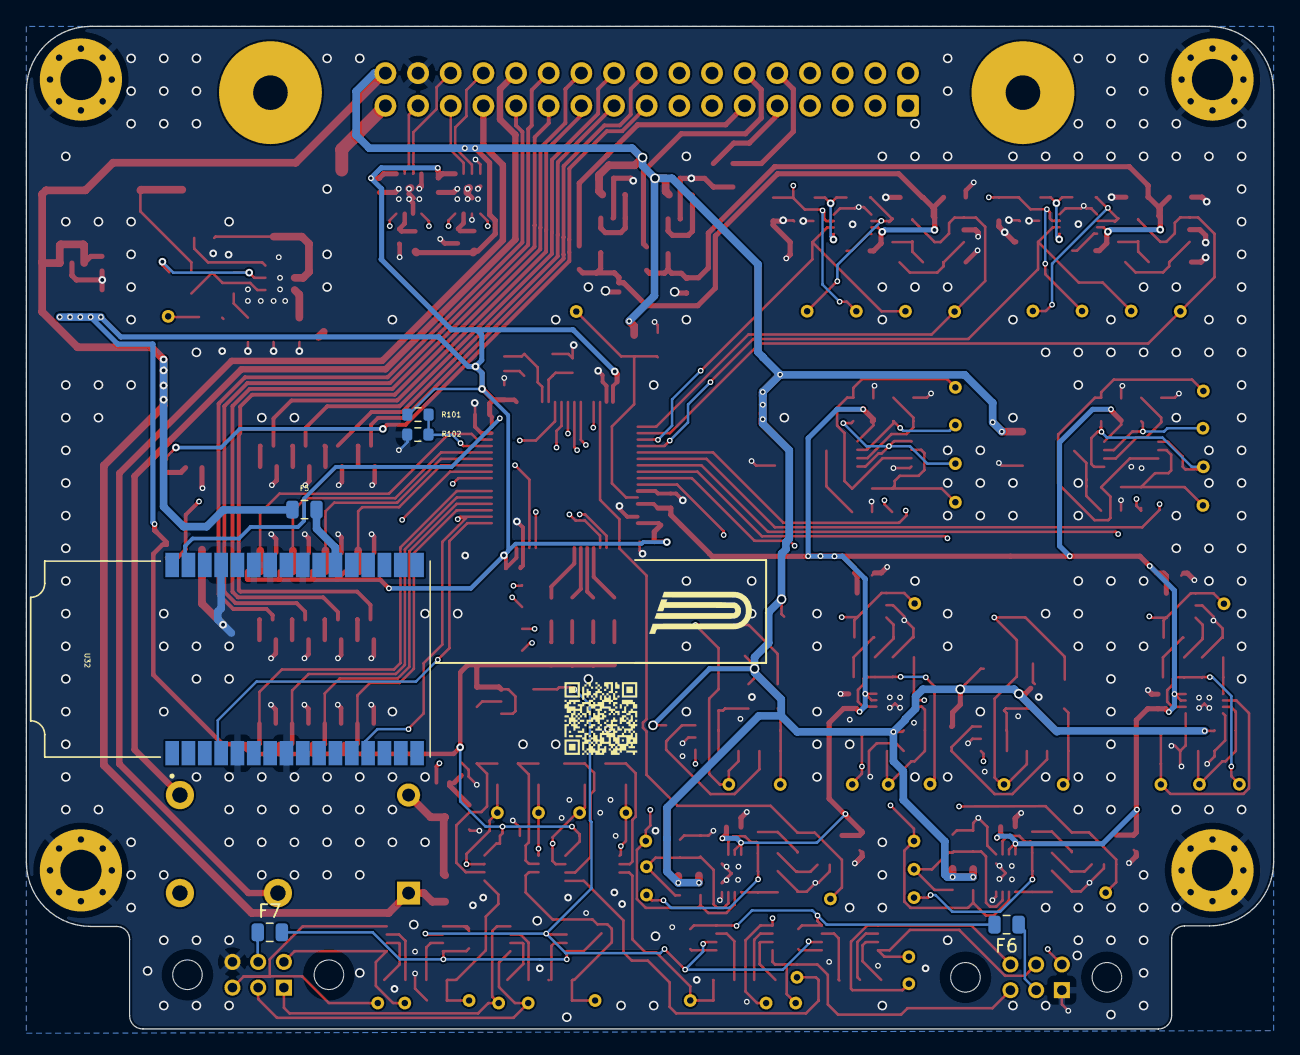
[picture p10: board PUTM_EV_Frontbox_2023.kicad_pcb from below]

Board: 4 copper layers, 97.0 x 78.0 mm, 320 parts (6 on the bottom side), 183 nets.

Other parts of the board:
C43, C44, C46, C47, C48, C49, C51, C52: 100n; C_0603_1608Metric_Pad1.08x0.95mm_HandSolder
C45, C50: 10n; C_0603_1608Metric_Pad1.08x0.95mm_HandSolder
C53: 10n; C_0603_1608Metric
C54, C55: 100n; C_0603_1608Metric
D8, D9: 24V; D_0603_1608Metric_Pad1.05x0.95mm_HandSolder
R61, R67: 100k; R_0603_1608Metric_Pad0.98x0.95mm_HandSolder
R62, R68: 0R; R_0603_1608Metric_Pad0.98x0.95mm_HandSolder
R63, R65, R66, R69, R71, R72: 4k7; R_0603_1608Metric_Pad0.98x0.95mm_HandSolder
R64, R70: 1k; R_0603_1608Metric_Pad0.98x0.95mm_HandSolder
R73, R106: 20k; R_0603_1608Metric
R74, R107: 10k; R_0603_1608Metric
TP21, TP25: APPS_P; TestPoint_THTPad_D1.0mm_Drill0.5mm
TP22, TP26: APPS_N; TestPoint_THTPad_D1.0mm_Drill0.5mm
TP23, TP27: APPS_MID; TestPoint_THTPad_D1.0mm_Drill0.5mm
TP24, TP28: APPS_OUT; TestPoint_THTPad_D1.0mm_Drill0.5mm
TP29, TP30: TestPoint_Small; TestPoint_THTPad_D1.0mm_Drill0.5mm
U10, U23: MCP6001-OT; SOT-23-5
U19, U21: MCP6N11-005; TDFN-8-1EP_3x2mm_P0.5mm_EP1.3x1.4mm
U20, U22: MCP6001; SOT-23-5
U31: STM32G484RETx; LQFP-64_10x10mm_P0.5mm

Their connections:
+3.3V: U31.1 (VBAT), U31.16 (VDD), U31.32 (VDD), U31.48 (VDD), U31.64 (VDD); also elsewhere on the board
+3.3VA: U31.29 (VDDA); also elsewhere on the board
+5V: C54.1, C55.1, U10.5 (V+), U23.5 (V+); also elsewhere on the board
/APPS1_3V3: C48.1, C49.1, R68.2, U21.7 (V+), U22.5 (V+); also elsewhere on the board
/APPS2_3V3: C43.1, C44.1, R62.2, U19.7 (V+), U20.5 (V+); also elsewhere on the board
/APPS_POT_1: D9.2 (A2), R67.1, TP25.1, U21.3 (+); also elsewhere on the board
/APPS_POT_2: D8.2 (A2), R61.1, TP21.1, U19.3 (+); also elsewhere on the board
/APPS_sig1: C52.2, TP28.1, U22.1, U22.4 (-), U31.18 (PA4)
/APPS_sig2: C47.2, TP24.1, U20.1, U20.4 (-), U31.17 (PA3)
/BRAKE_PRESSURE_FRONT_OUT: U31.22 (PC4); also elsewhere on the board
/BRAKE_PRESSURE_REAR_OUT: U31.21 (PA7); also elsewhere on the board
/CAN1_RX: U31.45 (PA11); also elsewhere on the board
/CAN1_TX: U31.46 (PA12); also elsewhere on the board
/CAN2_RX: U31.34 (PB12); also elsewhere on the board
/CAN2_TX: U31.35 (PB13); also elsewhere on the board
/DAC1_REF: C50.1, TP26.1, U21.2 (-), U31.20 (PA6)
/DAC2_REF: C45.1, TP22.1, U19.2 (-), U31.19 (PA5)
/DEBUG_LED1: U31.39 (PC7); also elsewhere on the board
/DEBUG_LED2: U31.38 (PC6); also elsewhere on the board
/DEBUG_LED3: U31.37 (PB15); also elsewhere on the board
/DEBUG_LED4: U31.36 (PB14); also elsewhere on the board
/GEARBOX_TEMP_1: U31.13 (PA1); also elsewhere on the board
/GEARBOX_TEMP_2: U31.14 (PA2); also elsewhere on the board
/HSE_IN: U31.5 (PF0); also elsewhere on the board
/HSE_OUT: U31.6 (PF1); also elsewhere on the board
/NRST: U31.7 (PG10); also elsewhere on the board
/STEERING_POSITION_2_OUT: U31.26 (PB2); also elsewhere on the board
/STEERING_POSITION_IN: U10.3 (+); also elsewhere on the board
/STEERING_POSITION_OUT: C53.1, R107.2, TP30.1, U23.1, U31.24 (PB0)
/SUSP_L_OUT: U31.23 (PC5); also elsewhere on the board
/SUSP_R_OUT: U31.25 (PB1); also elsewhere on the board
/SWCLK: U31.50 (PA14); also elsewhere on the board
/SWDIO: U31.49 (PA13); also elsewhere on the board
/Safety_control: U31.56 (PB3); also elsewhere on the board
/Sense_BSPD: U31.62 (PB9); also elsewhere on the board
/Sense_EBS: U31.52 (PC10); also elsewhere on the board
/Sense_Left_Wheel: U31.57 (PB4); also elsewhere on the board
/Sense_Right_Wheel: U31.58 (PB5); also elsewhere on the board
/Sense_driver: U31.54 (PC12); also elsewhere on the board
/Sense_inertia: U31.51 (PA15); also elsewhere on the board
/Sense_left: U31.53 (PC11); also elsewhere on the board
/Sense_overtravel: U31.59 (PB6); also elsewhere on the board
/Sense_right: U31.60 (PB7); also elsewhere on the board
/Tensometer 1: U31.8 (PC0); also elsewhere on the board
/Tensometer 2: U31.9 (PC1); also elsewhere on the board
/Tensometer 3: U31.10 (PC2); also elsewhere on the board
/Tensometer 4: U31.11 (PC3); also elsewhere on the board
/VREF: U31.28 (VREF+); also elsewhere on the board
GND: C43.2, C44.2, C45.2, C46.2, C48.2, C49.2, C50.2, C51.2, C54.2, C55.2, D8.1 (A1), D9.1 (A1), R61.2, R64.1, R67.2, R70.1, R74.2, R106.1, U10.2 (V-), U19.4 (V-), U19.5 (RF), U19.9 (EP), U20.2 (V-), U21.4 (V-), U21.5 (RF), U21.9 (EP), U22.2 (V-), U23.2 (V-), U31.15 (VSS), U31.27 (VSSA), U31.31 (VSS), U31.47 (VSS), U31.63 (VSS); also elsewhere on the board
unnamed: C47.1, R65.2, R66.1
unnamed: C52.1, R71.2, R72.1
unnamed: R63.2, R65.1, TP23.1, U19.6
unnamed: R69.2, R71.1, TP27.1, U21.6
unnamed: R73.1, U10.1, U10.4 (-)
unnamed: R62.1, U19.8 (EN)
unnamed: R63.1, R64.2, U19.1 (FG)
unnamed: C46.1, R66.2, U20.3 (+)
unnamed: R68.1, U21.8 (EN)
unnamed: R69.1, R70.2, U21.1 (FG)
unnamed: C51.1, R72.2, U22.3 (+)
unnamed: R73.2, R74.1, TP29.1, U23.3 (+)
unnamed: C53.2, R106.2, R107.1, U23.4 (-)
unnamed 173: U31.61 (PB8); also elsewhere on the board

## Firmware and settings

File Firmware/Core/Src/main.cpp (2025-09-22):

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
/* Includes ------------------------------------------------------------------*/
#include "main.h"
#include "cmsis_os.h"

/* USER CODE BEGIN Includes */
#include <stdlib.h>
#include <algorithm>
#include <cstdint>
#include <stdbool.h>
#include <math.h>

#include "interfaces/AppsAbstract.hpp"
#include "interfaces/BrakesAbstract.hpp"
#include "interfaces/AnalogsAbstract.hpp"
#include "interfaces/ScAbstract.hpp"
#include "interfaces/AccelerometerAbstract.hpp"
#include "interfaces/Tensometers.hpp"
#include "PUTM_EV_CAN_LIBRAR/lib/can_interface.hpp"

/* USER CODE END Includes */

/* USER CODE BEGIN PM */

uint16_t adc1_dma_buffer[400];
uint16_t adc2_dma_buffer[250];

bool rtd {false};
bool inverterStatus {false};
int status_s;
int status_d;
uint8_t errors_counter=0;

Apps apps;
Brakes brakes;
Analog analogs;
Accelerometer accelerometer;
SC sc;
Tensometers tensometers;

/* USER CODE END PM */

ADC_HandleTypeDef hadc1;
ADC_HandleTypeDef hadc2;
DMA_HandleTypeDef hdma_adc1;
DMA_HandleTypeDef hdma_adc2;

DAC_HandleTypeDef hdac1;
DAC_HandleTypeDef hdac2;

FDCAN_HandleTypeDef hfdcan1;
FDCAN_HandleTypeDef hfdcan2;

IWDG_HandleTypeDef hiwdg;

TIM_HandleTypeDef htim2;

/* Definitions for MainTask */
osThreadId_t MainTaskHandle;
const osThreadAttr_t MainTask_attributes = {
  .name = "MainTask",
  .stack_size = 128 * 16,
  .priority = (osPriority_t) osPriorityNormal
};
/* Definitions for BlinkTask */
osThreadId_t BlinkTaskHandle;
const osThreadAttr_t BlinkTask_attributes = {
  .name = "BlinkTask",
  .stack_size = 128 * 4,
  .priority = (osPriority_t) osPriorityLow
};
/* Definitions for AmkTask */
osThreadId_t AmkTaskHandle;
const osThreadAttr_t AmkTask_attributes = {
  .name = "AmkTask",
  .stack_size = 128 * 4,
  .priority = (osPriority_t) osPriorityLow
};
/* USER CODE BEGIN PV */
enum struct StateMachine {
	UNDEFINED = -1,
	ERROR_RESET,
	IDLING,
	STARTUP,
	TORQUE_CONTROL,
	SWITCH_OFF
};
StateMachine state = StateMachine::UNDEFINED;
/* USER CODE END PV */

void SystemClock_Config(void);
static void MX_GPIO_Init(void);
static void MX_DMA_Init(void);
static void MX_ADC1_Init(void);
static void MX_ADC2_Init(void);
static void MX_DAC1_Init(void);
static void MX_DAC2_Init(void);
static void MX_TIM2_Init(void);
static void MX_FDCAN1_Init(void);
static void MX_FDCAN2_Init(void);
static void MX_IWDG_Init(void);
void StartMainTask(void *argument);
void StartBlinkTask(void *argument);
void StartAmkTask(void *argument);

/* USER CODE BEGIN PFP */
void HAL_ADC_ConvCpltCallback(ADC_HandleTypeDef* hadc)
{
	uint8_t j = 0;
	if (hadc->Instance == ADC1)
	{
		int j = 0;
		for(int i = 0; i < 200; i = i+4)
		{
			apps.apps1_val_raw[j] = adc1_dma_buffer[i];
			analogs.steering_position_val_raw[j] = adc1_dma_buffer[i+1];
			tensometers.tensometer_1_val_raw[j]=adc1_dma_buffer[i+2];
			tensometers.tensometer_2_val_raw[j]=adc1_dma_buffer[i+3];
			j++;
		}
	}
	else
	{
		j = 0;
		for(int i = 0; i < 250; i = i+5)
		{
			apps.apps2_val_raw[j] = adc2_dma_buffer[i+4];
			analogs.steering_position2_val_raw[j] = adc2_dma_buffer[i+3];
			brakes.brake_pressure_rear_val_raw[j] = adc2_dma_buffer[i];
			brakes.brake_pressure_front_val_raw[j] = adc2_dma_buffer[i+1];
			j++;
		}
	}
}
/* USER CODE END PFP */

/* USER CODE BEGIN 0 */
uint16_t apps_value_to_send;
std::pair<uint16_t, uint16_t> brakePressureValueToSend;
int16_t steering_position_to_send;
int16_t steering_position_to_send2;
int16_t tensometers_to_send1;
int16_t tensometers_to_send2;
uint8_t sc_state;
/* USER CODE END 0 */

/**
  * @brief  The application entry point.
  * @retval int
  */
int main(void)
{

  /* MCU Configuration--------------------------------------------------------*/

  /* Reset of all peripherals, Initializes the Flash interface and the Systick. */
  HAL_Init();

  /* Configure the system clock */
  SystemClock_Config();

  /* Initialize all configured peripherals */
  MX_GPIO_Init();
  MX_DMA_Init();
  MX_ADC1_Init();
  MX_ADC2_Init();
  MX_DAC1_Init();
  MX_DAC2_Init();
  MX_TIM2_Init();
  MX_FDCAN1_Init();
  MX_FDCAN2_Init();

  //MX_IWDG_Init();

 // MX_IWDG_Init();

  /* Init scheduler */
  osKernelInitialize();

  /* USER CODE BEGIN RTOS_MUTEX */
  /* add mutexes, ... */
  /* USER CODE END RTOS_MUTEX */

  /* USER CODE BEGIN RTOS_SEMAPHORES */
  /* add semaphores, ... */
  /* USER CODE END RTOS_SEMAPHORES */

  /* USER CODE BEGIN RTOS_TIMERS */
  /* start timers, add new ones, ... */
  /* USER CODE END RTOS_TIMERS */

  /* USER CODE BEGIN RTOS_QUEUES */
  /* add queues, ... */
  /* USER CODE END RTOS_QUEUES */

  /* Create the thread(s) */
  /* creation of MainTask */
  MainTaskHandle = osThreadNew(StartMainTask, NULL, &MainTask_attributes);

  /* creation of BlinkTask */
  BlinkTaskHandle = osThreadNew(StartBlinkTask, NULL, &BlinkTask_attributes);

  /* creation of AmkTask */
 // AmkTaskHandle = osThreadNew(StartAmkTask, NULL, &AmkTask_attributes);

  /* USER CODE BEGIN RTOS_THREADS */
  /* add threads, ... */
  /* USER CODE END RTOS_THREADS */

  /* USER CODE BEGIN RTOS_EVENTS */
  /* add events, ... */
  /* USER CODE END RTOS_EVENTS */

  /* Start scheduler */
  osKernelStart();

  /* We should never get here as control is now taken by the scheduler */

  /* Infinite loop */
  /* USER CODE BEGIN WHILE */

  while (1)
  {
    /* USER CODE END WHILE */

    /* USER CODE BEGIN 3 */
  }
  /* USER CODE END 3 */
}

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
/* USER CODE BEGIN Header_StartMainTask */
/**
  * @brief  Function implementing the MainTask thread.
  * @param  argument: Not used
  * @retval None
  */
/* USER CODE END Header_StartMainTask */
void StartMainTask(void *argument)
{
  /* USER CODE BEGIN 5 */
	/* Set APPS reference voltage */
	HAL_DAC_Start(&hdac1, DAC_CHANNEL_2);
	HAL_DAC_Start(&hdac2, DAC_CHANNEL_1);
	HAL_DAC_SetValue(&hdac1, DAC_CHANNEL_2, DAC_ALIGN_12B_R, 1950); // ~2200  mV 2733// 1,5714V
	HAL_DAC_SetValue(&hdac2, DAC_CHANNEL_1, DAC_ALIGN_12B_R, 2100); // ~2418 mV 3003// 1,6923V

	HAL_GPIO_WritePin(BOOOT_GPIO_Port, BOOOT_Pin, GPIO_PIN_RESET);
	// APPS
	HAL_ADCEx_Calibration_Start(&hadc1, ADC_SINGLE_ENDED);
	HAL_ADCEx_Calibration_Start(&hadc2, ADC_SINGLE_ENDED);

	HAL_ADC_Start_DMA(&hadc1, reinterpret_cast<uint32_t*>(adc1_dma_buffer), 200);
	HAL_ADC_Start_DMA(&hadc2, reinterpret_cast<uint32_t*>(adc2_dma_buffer), 250);
	HAL_TIM_Base_Start(&htim2);

	HAL_FDCAN_Start(&hfdcan1);
	HAL_FDCAN_ActivateNotification(&hfdcan1, FDCAN_IT_RX_FIFO0_NEW_MESSAGE, 0);

//	HAL_FDCAN_Start(&hfdcan2);
//	HAL_FDCAN_ActivateNotification(&hfdcan2, FDCAN_IT_RX_FIFO0_NEW_MESSAGE, 0);

	HAL_GPIO_WritePin(LED1_GPIO_Port, LED1_Pin, GPIO_PIN_SET);
	HAL_GPIO_WritePin(LED2_GPIO_Port, LED2_Pin, GPIO_PIN_SET);
	HAL_GPIO_WritePin(LED3_GPIO_Port, LED3_Pin, GPIO_PIN_SET);
	HAL_GPIO_WritePin(LED4_GPIO_Port, LED4_Pin, GPIO_PIN_SET);
	/* Infinite loop */
	for(;;)
	{
		osDelay(12);

		apps_value_to_send = apps.get_value_to_send();
		brakePressureValueToSend = brakes.get_raw_avg_press_value();
		steering_position_to_send = analogs.get_steering_position();
		steering_position_to_send2 = analogs.get_steering_position2();
		tensometers_to_send1=tensometers.get_tens_1();
		tensometers_to_send2=tensometers.get_tens_2();

		PUTM_CAN::DriverInput drvInput = {
			  .pedalPosition = apps_value_to_send,
			  .brakePressureFront = brakePressureValueToSend.first,
			  .brakePressureRear = brakePressureValueToSend.second,
			  .steeringWheelPosition = (int16_t)steering_position_to_send
		};

	//	if (HAL_FDCAN_GetTxFifoFreeLevel(&hfdcan1) >=2) {

			auto driverInputFrame = PUTM_CAN::Can_tx_message<PUTM_CAN::DriverInput>(drvInput, PUTM_CAN::can_tx_header_DRIVER_INPUT);
			HAL_StatusTypeDef status = driverInputFrame.send(hfdcan1);
			status_s=status;
			UNUSED(status);

		//}

		sc_state = sc.update_val();

		PUTM_CAN::FrontData frontData = {
					  .sense_left_kill    = !(static_cast<bool>((sc_state>>1) & 1)),
					  .sense_right_kill   = !(static_cast<bool>((sc_state>>0) & 1)),
					  .sense_driver_kill  = !(static_cast<bool>((sc_state>>2) & 1)),
					  .sense_inertia      = !(static_cast<bool>((sc_state>>3) & 1)),
					  .sense_bspd         = !(static_cast<bool>((sc_state>>4) & 1)),
					  .sense_overtravel   = !(static_cast<bool>((sc_state>>5) & 1)),
					  .safety_suspension_fl  = 0,//(static_cast<bool>((sc_state>>6) & 1)),
					  .safety_suspension_fr  = 0,//static_cast<bool>((sc_state>>7) & 1),

		};
		if (brakePressureValueToSend.first > brakes.FRONT_BRAKING_THRESHOLD || brakePressureValueToSend.second > brakes.REAR_BRAKING_THRESHOLD)
		{
			frontData.is_braking = true;
		}
		frontData.apps=static_cast<bool>(apps.apps_flag & 1);
		//frontData.apps_implausibility=(uint8_t)(apps.diff *10);// sending apps implausibility with 1 place decimal
		frontData.frontLeftSuspension=tensometers_to_send1;
		frontData.frontRightSuspension=tensometers_to_send2;

		osDelay(12);


	  	auto frontDataFrame =  PUTM_CAN::Can_tx_message<PUTM_CAN::FrontData>(frontData, PUTM_CAN::can_tx_header_FRONT_DATA);
	  	status = frontDataFrame.send(hfdcan1);
	  	status_d=status;



		if(status_d || status_s == HAL_ERROR)
		{
			//HAL_GPIO_WritePin(LED4_GPIO_Port, LED4_Pin, GPIO_PIN_RESET);
			NVIC_SystemReset();
		}

	  /*	switch (status)
		{

		case HAL_OK:
			HAL_GPIO_WritePin(LED3_GPIO_Port, LED3_Pin,  GPIO_PIN_RESET);
			HAL_GPIO_WritePin(LED2_GPIO_Port, LED2_Pin,  GPIO_PIN_RESET);
		case HAL_ERROR:
			HAL_GPIO_WritePin(LED3_GPIO_Port, LED3_Pin,  GPIO_PIN_RESET);
			HAL_GPIO_WritePin(LED2_GPIO_Port, LED2_Pin,  GPIO_PIN_SET);
		case 2:
			HAL_GPIO_WritePin(LED3_GPIO_Port, LED3_Pin,  GPIO_PIN_SET);
			HAL_GPIO_WritePin(LED2_GPIO_Port, LED2_Pin,  GPIO_PIN_SET);
		}
*/
		HAL_IWDG_Refresh(&hiwdg);
//	  	osDelay(25);
  }
  /* USER CODE END 5 */
}

/* USER CODE BEGIN Header_StartBlinkTask */
PUTM_CAN::PcMainData pcMain;
/**
* @brief Function implementing the BlinkTask thread.
* @param argument: Not used
* @retval None
*/
/* USER CODE END Header_StartBlinkTask */
void StartBlinkTask(void *argument)
{
  /* USER CODE BEGIN StartBlinkTask */
  /* Infinite loop */
	osDelay(500);
	for(;;)
	{
		PUTM_CAN::Dashboard dsh{0};
		// Gimela 26.02 reciving RTD signal from PC to chceck it state
		PUTM_CAN::PcMainData pcMain;
		if(PUTM_CAN::can.get_pc_new_data())
		{
			auto pcMain = PUTM_CAN::can.get_pc_main_data();
			auto rtd_state=pcMain.rtd;
			rtd=rtd_state;
		}


		if (PUTM_CAN::can.get_dashboard_new_data())
		{
			auto dash_rtd_button = PUTM_CAN::can.get_dashboard().ready_to_drive_button;

			/* Check if we want to enable TS voltage*/ //no need to check if we send signal from computer
		/*	if (dash_ts_button == true)
			{
				dsh.ts_activation_button = 1;
				HAL_GPIO_WritePin(LED2_GPIO_Port, LED2_Pin, GPIO_PIN_RESET);
			}
*/
			/* Act according to current rtd state */
//			switch(rtd){
//			case true:
//				if (dash_rtd_button == true)
//				{
//					/* Escape rtd */
//					rtd = false;
//				}
//				break;
//
//			case false:
//				/* If NOT in rtd, check if we want to enter it */
//				if (dash_rtd_button == true and brakePressureValueToSend.first >= brakes.FRONT_BRAKING_THRESHOLD and brakePressureValueToSend.second >= brakes.REAR_BRAKING_THRESHOLD)
//				{
//					/* Enter rtd */
//					rtd = true;
//					HAL_GPIO_WritePin(LED2_GPIO_Port, LED2_Pin, GPIO_PIN_RESET);
//				}
//				break;
//			}
//			pcMain.rtd = rtd;
		}
		osDelay(50);
		HAL_GPIO_WritePin(LED2_GPIO_Port, LED2_Pin, GPIO_PIN_SET);
		HAL_GPIO_TogglePin(LED1_GPIO_Port, LED1_Pin);
		HAL_IWDG_Refresh(&hiwdg);

//		auto amkRearLeftData = PUTM_CAN::can.get_amk_rear_left_actual_values2();
//		auto amkRearRightData = PUTM_CAN::can.get_amk_rear_right_actual_values2();
//
//		auto amkRearLeftMain = PUTM_CAN::can.get_amk_rear_left_actual_values1();
//		auto amkRearRightMain = PUTM_CAN::can.get_amk_rear_right_actual_values1();
//
//		auto tsVoltage = PUTM_CAN::can.get_bms_hv_main().voltage_sum;
//
//		pcMain.invertersReady = inverterStatus;
//		pcMain.rearLeftInverterTemperature = amkRearLeftData.AMK_TempIGBT / 10;
//		pcMain.rearRightInverterTemperature = amkRearRightData.AMK_TempIGBT / 10;
//		pcMain.rearLeftMotorTemperature = amkRearLeftData.AMK_TempMotor / 10;
//		pcMain.rearRightMotorTemperature = amkRearRightData.AMK_TempMotor / 10;
//		pcMain.rtd = rtd;
//		pcMain.power = ((amkRearLeftMain.AMK_TorqueCurrent * 107.20) / 16384) + ((amkRearRightMain.AMK_TorqueCurrent * 107.20) / 16384) * tsVoltage;
//		float rpm = (amkRearLeftMain.AMK_ActualVelocity + amkRearRightMain.AMK_ActualVelocity)/2.0;
//		pcMain.vehicleSpeed = ((amkRearLeftMain.AMK_ActualVelocity + amkRearRightMain.AMK_ActualVelocity)/2) * 60 * 2 * 3.14 * (405.0/2.0) * 0.0000001;
//		pcMain.rpm = (uint32_t)rpm;

//		auto pc_main = PUTM_CAN::Can_tx_message<PUTM_CAN::PcMainData>(pcMain, PUTM_CAN::can_tx_header_PC_MAIN_DATA);
//		auto status = pc_main.send(hfdcan1);
//		UNUSED(status);


		//auto dash = PUTM_CAN::Can_tx_message<PUTM_CAN::Dashboard>(dsh, PUTM_CAN::can_tx_header_DASHBOARD); // Now send by computer
		//dsh.ts_activation_button = 0;
	//	auto status = dash.send(hfdcan1);
	//	UNUSED(status);

	}
  /* USER CODE END StartBlinkTask */
}

/* USER CODE BEGIN Header_StartAmkTask */

/**
* @brief Function implementing the AmkTask thread.
* @param argument: Not used
* @retval None
*/
/* USER CODE END Header_StartAmkTask */
void StartAmkTask(void *argument)
{
  /* USER CODE BEGIN StartAmkTask */
  /* Infinite loop */

	PUTM_CAN::AmkFrontLeftSetpoints1  frontLeftAmkSetpoints = {};
	PUTM_CAN::AmkFrontRightSetpoints1 frontRightAmkSetpoints = {};
	PUTM_CAN::AmkRearLeftSetpoints1   rearLeftAmkSetpoints = {};
	PUTM_CAN::AmkRearRightSetpoints1  rearRightAmkSetpoints = {};

	uint32_t timeout = 0;
	constexpr uint32_t amk_startup_timeout = 5000;

	PUTM_CAN::PcMainData pcMain = {
		  .rtd = rtd,
	};

	for(;;)
	{
		auto frontLeftAmk  = PUTM_CAN::can.get_amk_front_left_actual_values1();
		auto frontRightAmk = PUTM_CAN::can.get_amk_front_right_actual_values1();
		auto rearLeftAmk   = PUTM_CAN::can.get_amk_rear_left_actual_values1();
		auto rearRightAmk  = PUTM_CAN::can.get_amk_rear_right_actual_values1();

	switch(state)
	{
		case StateMachine::UNDEFINED:
		{
		  if (frontLeftAmk.AMK_Status.AMK_bError || frontRightAmk.AMK_Status.AMK_bError || rearLeftAmk.AMK_Status.AMK_bError || rearRightAmk.AMK_Status.AMK_bError )
		  {
	        state = StateMachine::ERROR_RESET;
	      }
	      if (frontLeftAmk.AMK_Status.AMK_bSystemReady && frontRightAmk.AMK_Status.AMK_bSystemReady && rearLeftAmk.AMK_Status.AMK_bSystemReady && rearRightAmk.AMK_Status.AMK_bSystemReady)
	      {
	    	  state = StateMachine::IDLING;
	      }
		}
	    break;
		case StateMachine::ERROR_RESET:
		{
		      if (frontLeftAmk.AMK_Status.AMK_bSystemReady && frontRightAmk.AMK_Status.AMK_bSystemReady && rearLeftAmk.AMK_Status.AMK_bSystemReady && rearRightAmk.AMK_Status.AMK_bSystemReady)
		      {
		    	frontLeftAmkSetpoints.AMK_Control.AMK_bErrorReset = false;
		    	frontRightAmkSetpoints.AMK_Control.AMK_bErrorReset = false;
		    	rearLeftAmkSetpoints.AMK_Control.AMK_bErrorReset = false;
		    	rearRightAmkSetpoints.AMK_Control.AMK_bErrorReset = false;
		        state = StateMachine::IDLING;
		      }
		      else
		      {
		    	frontLeftAmkSetpoints.AMK_Control.AMK_bErrorReset = true;
		    	frontRightAmkSetpoints.AMK_Control.AMK_bErrorReset = true;
			    rearLeftAmkSetpoints.AMK_Control.AMK_bErrorReset = true;
			    rearRightAmkSetpoints.AMK_Control.AMK_bErrorReset = true;
		      }
		}
		break;
		case StateMachine::IDLING:
		{
			inverterStatus = false;
			if ((frontLeftAmk.AMK_Status.AMK_bError or frontRightAmk.AMK_Status.AMK_bError or rearLeftAmk.AMK_Status.AMK_bError  or rearRightAmk.AMK_Status.AMK_bError))
			{
//				state = StateMachine::ERROR_RESET;
			}
			if (rtd == true)
			{
				state = StateMachine::STARTUP;
				timeout = xTaskGetTickCount();
			}
		}
		break;

		case StateMachine::STARTUP:
		{
			 if ((xTaskGetTickCount() - timeout) > amk_startup_timeout)
			 {
				 /* Stop startup and go to idle through error reset */
				 state = StateMachine::SWITCH_OFF;
				 rtd = false;
				 timeout = 0;
			 }
			 if ((frontLeftAmk.AMK_Status.AMK_bError or frontRightAmk.AMK_Status.AMK_bError or rearLeftAmk.AMK_Status.AMK_bError or rearRightAmk.AMK_Status.AMK_bError))
			 {
				 state = StateMachine::ERROR_RESET;
			 }

			 frontLeftAmkSetpoints.AMK_Control.AMK_bDcOn = true;
			 frontRightAmkSetpoints.AMK_Control.AMK_bDcOn = true;
			 rearLeftAmkSetpoints.AMK_Control.AMK_bDcOn = true;
			 rearRightAmkSetpoints.AMK_Control.AMK_bDcOn = true;

			 frontLeftAmkSetpoints.AMK_TorqueLimitNegativ  = 0;
			 frontRightAmkSetpoints.AMK_TorqueLimitNegativ = 0;
			 rearLeftAmkSetpoints.AMK_TorqueLimitNegativ   = 0;
			 rearRightAmkSetpoints.AMK_TorqueLimitNegativ  = 0;

			 frontLeftAmkSetpoints.AMK_TorqueLimitPositiv  = 0;
			 frontRightAmkSetpoints.AMK_TorqueLimitPositiv = 0;
			 rearLeftAmkSetpoints.AMK_TorqueLimitPositiv   = 0;
			 rearRightAmkSetpoints.AMK_TorqueLimitPositiv  = 0;

			 frontLeftAmkSetpoints.AMK_TargetVelocity  = 0;
			 frontRightAmkSetpoints.AMK_TargetVelocity = 0;
			 rearLeftAmkSetpoints.AMK_TargetVelocity   = 0;
			 rearRightAmkSetpoints.AMK_TargetVelocity  = 0;


			 if (!frontLeftAmk.AMK_Status.AMK_bDcOn && !frontRightAmk.AMK_Status.AMK_bDcOn && !rearLeftAmk.AMK_Status.AMK_bDcOn && !rearRightAmk.AMK_Status.AMK_bDcOn)
			 {
			     break;
			 }

			 frontLeftAmkSetpoints.AMK_Control.AMK_bInverterOn = true;
			 frontRightAmkSetpoints.AMK_Control.AMK_bInverterOn = true;
			 rearLeftAmkSetpoints.AMK_Control.AMK_bInverterOn = true;
			 rearRightAmkSetpoints.AMK_Control.AMK_bInverterOn = true;

			 frontLeftAmkSetpoints.AMK_Control.AMK_bEnable = true;
			 frontRightAmkSetpoints.AMK_Control.AMK_bEnable = true;
			 rearLeftAmkSetpoints.AMK_Control.AMK_bEnable = true;
			 rearRightAmkSetpoints.AMK_Control.AMK_bEnable = true;

			 if (!frontLeftAmk.AMK_Status.AMK_bInverterOn && !frontRightAmk.AMK_Status.AMK_bInverterOn  && !rearLeftAmk.AMK_Status.AMK_bInverterOn  && !rearRightAmk.AMK_Status.AMK_bInverterOn )
			 {
			     break;
			 }
			 if (!(frontLeftAmk.AMK_Status.AMK_bQuitInverterOn && frontRightAmk.AMK_Status.AMK_bQuitInverterOn && rearLeftAmk.AMK_Status.AMK_bQuitInverterOn  && rearRightAmk.AMK_Status.AMK_bQuitInverterOn))
			 {
			     break;
			 }
			 else
			 {
				 /* Lastly, check if driver is not pressing acceleration pedal */
				 if (apps_value_to_send > 0)
				 {
					 break;
				 }
				 else
				 {
					 state = StateMachine::TORQUE_CONTROL;
					 HAL_GPIO_WritePin(LED3_GPIO_Port, LED3_Pin, GPIO_PIN_RESET);
				 }
			 }
		}
		break;

		case StateMachine::TORQUE_CONTROL:
		{
			/* Check some stop conditions*/
			if ((frontLeftAmk.AMK_Status.AMK_bError or frontRightAmk.AMK_Status.AMK_bError or rearLeftAmk.AMK_Status.AMK_bError or rearRightAmk.AMK_Status.AMK_bError))
			{
				state = StateMachine::SWITCH_OFF;
				rtd = false;
				break;
			}

			inverterStatus = true;

			frontLeftAmkSetpoints.AMK_TorqueLimitNegativ  = -1000;
			frontRightAmkSetpoints.AMK_TorqueLimitNegativ = -1000;
			rearLeftAmkSetpoints.AMK_TorqueLimitNegativ   = -1000;
			rearRightAmkSetpoints.AMK_TorqueLimitNegativ  = -1000;

			frontLeftAmkSetpoints.AMK_TorqueLimitPositiv  = 1000;
			frontRightAmkSetpoints.AMK_TorqueLimitPositiv = 1000;
			rearLeftAmkSetpoints.AMK_TorqueLimitPositiv   = 1000;
			rearRightAmkSetpoints.AMK_TorqueLimitPositiv  = 1000;

			float target_torque = (apps_value_to_send / 500.0) * 1000;

//			if (brakePressureValueToSend.first > 500 and frontLeftAmk.AMK_ActualVelocity > 0)
//			{
//				target_torque = -20.f;
//			}

			frontLeftAmkSetpoints.AMK_TargetVelocity  =  -1.0 * target_torque * 0.7;
			frontRightAmkSetpoints.AMK_TargetVelocity = target_torque * 0.7;
			rearLeftAmkSetpoints.AMK_TargetVelocity   = target_torque;
			rearRightAmkSetpoints.AMK_TargetVelocity  = -1.0  * target_torque;

			if (!rtd)
			{
				state = StateMachine::SWITCH_OFF;
				osDelay(10);
				break;
			}
		}
		break;

		case StateMachine::SWITCH_OFF:
		{

			frontLeftAmkSetpoints.AMK_Control.AMK_bInverterOn = false;
			frontRightAmkSetpoints.AMK_Control.AMK_bInverterOn = false;
			rearLeftAmkSetpoints.AMK_Control.AMK_bInverterOn = false;
			rearRightAmkSetpoints.AMK_Control.AMK_bInverterOn = false;

			frontLeftAmkSetpoints.AMK_Control.AMK_bEnable = false;
			frontRightAmkSetpoints.AMK_Control.AMK_bEnable = false;
			rearLeftAmkSetpoints.AMK_Control.AMK_bEnable = false;
			rearRightAmkSetpoints.AMK_Control.AMK_bEnable = false;

			frontLeftAmkSetpoints.AMK_Control.AMK_bDcOn = false;
			frontRightAmkSetpoints.AMK_Control.AMK_bDcOn = false;
			rearLeftAmkSetpoints.AMK_Control.AMK_bDcOn = false;
			rearRightAmkSetpoints.AMK_Control.AMK_bDcOn = false;

			if ((frontLeftAmk.AMK_Status.AMK_bError or frontRightAmk.AMK_Status.AMK_bError or rearLeftAmk.AMK_Status.AMK_bError  or rearRightAmk.AMK_Status.AMK_bError))
			{
//				state = StateMachine::ERROR_RESET;
			}

			/* Wait until inverter 0 is switched-off.*/
			if (frontLeftAmk.AMK_Status.AMK_bInverterOn || frontRightAmk.AMK_Status.AMK_bInverterOn || rearLeftAmk.AMK_Status.AMK_bInverterOn || rearRightAmk.AMK_Status.AMK_bInverterOn)
			{
				break;
			}
			state = StateMachine::IDLING;
		}
		break;
		default:
		{

		}
		break;
	}

	auto frontLeftSetpoint  = PUTM_CAN::Can_tx_message<PUTM_CAN::AmkFrontLeftSetpoints1  > (frontLeftAmkSetpoints,  PUTM_CAN::can_tx_header_AMK_FRONT_LEFT_SETPOINTS);
	auto frontRightSetpoint = PUTM_CAN::Can_tx_message<PUTM_CAN::AmkFrontRightSetpoints1 > (frontRightAmkSetpoints, PUTM_CAN::can_tx_header_AMK_FRONT_RIGHT_SETPOINTS);
	auto rearLefttSetpoint  = PUTM_CAN::Can_tx_message<PUTM_CAN::AmkRearLeftSetpoints1   > (rearLeftAmkSetpoints,   PUTM_CAN::can_tx_header_AMK_REAR_LEFT_SETPOINTS);
	auto rearRightSetpoint  = PUTM_CAN::Can_tx_message<PUTM_CAN::AmkRearRightSetpoints1  > (rearRightAmkSetpoints,  PUTM_CAN::can_tx_header_AMK_REAR_RIGHT_SETPOINTS);
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

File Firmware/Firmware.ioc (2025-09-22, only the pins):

Mcu.UserName=STM32G484RETx
PA11.Signal=FDCAN1_RX
PA12.Signal=FDCAN1_TX
PA13.Signal=SYS_JTMS-SWDIO
PA14.Signal=SYS_JTCK-SWCLK
PA15.GPIO_Label=Sense_Inertia
PA15.Signal=GPIO_Input
PA3.Signal=ADC1_IN4
PA4.Signal=ADC2_IN17
PA5.Signal=COMP_DAC12_group
PA6.Signal=COMP_DAC21_group
PA7.Signal=ADC2_IN4
PB0.Signal=ADC1_IN15
PB12.Signal=FDCAN2_RX
PB13.Signal=FDCAN2_TX
PB14.GPIO_Label=LED4
PB14.Signal=GPIO_Output
PB15.GPIO_Label=LED3
PB15.Signal=GPIO_Output
PB2.Signal=ADC2_IN12
PB3.GPIO_Label=SAFETY
PB3.Signal=GPIO_Output
PB4.GPIO_Label=Sense_Left_Wheel
PB4.Signal=GPIO_Input
PB5.GPIO_Label=Sense_Right_Wheel
PB5.Signal=GPIO_Input
PB6.GPIO_Label=Sense_Overtravel
PB6.Signal=GPIO_Input
PB7.GPIO_Label=Sense_Right_Kill
PB7.Signal=GPIO_Input
PB8-BOOT0.GPIO_Label=BOOOT
PB8-BOOT0.Signal=GPIO_Output
PB9.GPIO_Label=Sense_BSPD
PB9.Signal=GPIO_Input
PC10.GPIO_Label=Sense_EBS
PC10.Signal=GPIO_Input
PC11.GPIO_Label=Sense_Left
PC11.Signal=GPIO_Input
PC12.GPIO_Label=Sense_Driver
PC12.Signal=GPIO_Input
PC4.Signal=ADC2_IN5
PC5.Signal=ADC2_IN11
PC6.GPIO_Label=LED2
PC6.Signal=GPIO_Output
PC7.GPIO_Label=LED1
PC7.Signal=GPIO_Output
PF0-OSC_IN.Signal=RCC_OSC_IN
PF1-OSC_OUT.Signal=RCC_OSC_OUT

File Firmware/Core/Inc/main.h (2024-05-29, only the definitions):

#define LED4_Pin GPIO_PIN_14
#define LED4_GPIO_Port GPIOB
#define LED3_Pin GPIO_PIN_15
#define LED3_GPIO_Port GPIOB
#define LED2_Pin GPIO_PIN_6
#define LED2_GPIO_Port GPIOC
#define LED1_Pin GPIO_PIN_7
#define LED1_GPIO_Port GPIOC
#define Sense_Inertia_Pin GPIO_PIN_15
#define Sense_Inertia_GPIO_Port GPIOA
#define Sense_EBS_Pin GPIO_PIN_10
#define Sense_EBS_GPIO_Port GPIOC
#define Sense_Left_Pin GPIO_PIN_11
#define Sense_Left_GPIO_Port GPIOC
#define Sense_Driver_Pin GPIO_PIN_12
#define Sense_Driver_GPIO_Port GPIOC
#define SAFETY_Pin GPIO_PIN_3
#define SAFETY_GPIO_Port GPIOB
#define Sense_Left_Wheel_Pin GPIO_PIN_4
#define Sense_Left_Wheel_GPIO_Port GPIOB
#define Sense_Right_Wheel_Pin GPIO_PIN_5
#define Sense_Right_Wheel_GPIO_Port GPIOB
#define Sense_Overtravel_Pin GPIO_PIN_6
#define Sense_Overtravel_GPIO_Port GPIOB
#define Sense_Right_Kill_Pin GPIO_PIN_7
#define Sense_Right_Kill_GPIO_Port GPIOB
#define BOOOT_Pin GPIO_PIN_8
#define BOOOT_GPIO_Port GPIOB
#define Sense_BSPD_Pin GPIO_PIN_9
#define Sense_BSPD_GPIO_Port GPIOB

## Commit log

2023-02-26 Drafted the schematic
    [Diagnostic_port.kicad_pcb, Diagnostic_port.kicad_sch, PUTM_EV_Frontbox_2023.kicad_pcb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]
2023-03-07 Added power section, replaced SWPS
    [PUTM_EV_Frontbox_2023.kicad_sch, brake_pressure.kicad_sch, can_bus.kicad_sch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]
2023-03-10 Added MCU wiring
    [PUTM_EV_Frontbox_2023.kicad_sch, additional_analog.kicad_sch, apps.kicad_sch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]
2023-03-11 Schematic ready for review
    [Diagnostic_port.kicad_sch, PUTM_EV_Frontbox_2023.kicad_sch, additional_analog.kicad_sch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]
2023-03-30 Fixed all issues
    [Diagnostic_port.kicad_sch, PUTM_EV_Frontbox_2023.kicad_sch, additional_analog.kicad_sch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]
2023-04-01 Added missing laptimer resistor
    [PUTM_EV_Frontbox_2023.kicad_sch, additional_analog.kicad_sch, imu_sensor.kicad_sch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]
2023-04-19 Schematic modified, footprints assigned
    [PUTM_EV_Frontbox_2023.kicad_sch, additional_analog.kicad_sch, apps.kicad_sch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]
2023-04-19 Grouped components
    [PUTM_EV_Frontbox_2023.kicad_pcb, PUTM_EV_Frontbox_2023.kicad_sch, can_bus.kicad_sch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]
2023-04-21 Footprints placed, some routing
    [PUTM_EV_Frontbox_2023.kicad_pcb, PUTM_EV_Frontbox_2023.kicad_sch, power_section.kicad_sch]
2023-04-28 Redid component placement
    [Diagnostic_port.kicad_sch, PUTM_EV_Frontbox_2023.kicad_pcb, PUTM_EV_Frontbox_2023.kicad_sch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]
2023-04-28 Finished most of the routing
    [PUTM_EV_Frontbox_2023.kicad_pcb, PUTM_EV_Frontbox_2023.kicad_sch, safety_sense.kicad_sch]
2023-04-29 Layout mostly done
    [Diagnostic_port.kicad_pcb, Diagnostic_port.kicad_sch, PUTM_EV_Frontbox_2023.kicad_pcb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]
2023-05-01 Ready for production
    [Diagnostic_port.kicad_pcb, PUTM_EV_Frontbox_2023.kicad_pcb, PUTM_EV_Frontbox_2023.kicad_sch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]
2023-05-16 Written firmware
    [PUTM_EV_Frontbox_2023.kicad_sch, apps1.kicad_sch]
2023-10-02 PCB taken apart
    [APPS1.kicad_sch, PUTM_EV_Frontbox_2023.kicad_pcb, PUTM_EV_Frontbox_2023.kicad_sch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]
2023-10-02 Merged branch new_apps
    [APPS1.kicad_sch, PUTM_EV_Frontbox_2023.kicad_sch, suspension.kicad_sch]
2023-10-05 Added additional analog measurement ciructry
    [PUTM_EV_Frontbox_2023.kicad_sch, suspension_potentiometer.kicad_sch]
2023-10-05 Updated PCB
    [APPS1.kicad_sch, PUTM_EV_Frontbox_2023.kicad_pcb]
2023-10-05 Schematic updates
    [APPS1.kicad_sch, PUTM_EV_Frontbox_2023.kicad_pcb, PUTM_EV_Frontbox_2023.kicad_sch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]
2023-10-09 Started PCB layout
    [APPS2.kicad_sch, APPS21.kicad_sch, PUTM_EV_Frontbox_2023.kicad_pcb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]
2023-10-17 Changed board outline and layout to match ASB
    [APPS1.kicad_sch, PUTM_EV_Frontbox_2023.kicad_pcb, PUTM_EV_Frontbox_2023.kicad_sch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]
2023-10-17 Removed APPS pots
    [APPS1.kicad_sch, APPS2.kicad_sch, PUTM_EV_Frontbox_2023.kicad_pcb]
2023-10-28 Changed mcu pinout
    [PUTM_EV_Frontbox_2023.kicad_pcb, PUTM_EV_Frontbox_2023.kicad_sch, imu_sensor.kicad_sch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]
2023-10-28 Changed analog section
    [PUTM_EV_Frontbox_2023.kicad_pcb]
2023-10-29 routing done
    [PUTM_EV_Frontbox_2023.kicad_pcb, PUTM_EV_Frontbox_2023.kicad_sch, can_bus.kicad_sch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]
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2023-11-08 Board review
    [PUTM_EV_Frontbox_2023.kicad_pcb, PUTM_EV_Frontbox_2023.kicad_sch]
2023-11-14 Moved sw cap closer to pins
    [PUTM_EV_Frontbox_2023.kicad_pcb, PUTM_EV_Frontbox_2023.kicad_sch, safety_sense.kicad_sch]
2023-11-17 Production files
    [PUTM_EV_Frontbox_2023.kicad_pcb, power_section.kicad_sch]
2024-02-11 New firmware
    [PUTM_EV_Frontbox_2023.kicad_pcb, PUTM_EV_Frontbox_2023.kicad_sch, power_section.kicad_sch]
2024-02-17 Added gearbox temperature sensors on schematic
    [APPS1.kicad_sch, PUTM_EV_Frontbox_2023.kicad_pcb, PUTM_EV_Frontbox_2023.kicad_sch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]
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2024-03-02 fixing board
2024-03-02 hardware reset
    [APPS1.kicad_sch, APPS2.kicad_sch, APPS21.kicad_sch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]
2024-03-02 Added production hardware
    [APPS1.kicad_sch, APPS2.kicad_sch, APPS21.kicad_sch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]
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2024-03-20 Removed hardware from repo
    [APPS1.kicad_sch, APPS2.kicad_sch, APPS21.kicad_sch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]
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2024-05-29 rework sc data return
    [Sc.cpp]
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2024-06-12 Rework steering sensor analog data
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2024-06-14 Fix adc2 buffer size
    [Firmware.ioc, main.cpp]
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2024-08-25 Correct motor order
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2024-09-03 Add hardware to repo
    [APPS1.kicad_sch, APPS2.kicad_sch, APPS21.kicad_sch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]
2024-09-03 Move hardware to higher directory
    [APPS1.kicad_sch, APPS2.kicad_sch, APPS21.kicad_sch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]
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2024-10-19 dash can message fix
    [main.cpp]
2024-11-15 Added current PCB layout
    [APPS1.kicad_sch, APPS2.kicad_sch, APPS21.kicad_sch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]
2024-12-01 Changes in current layout, added tensometers to layout
    [PUTM_EV_Frontbox_2023.kicad_pcb, PUTM_EV_Frontbox_2023.kicad_sch, Tensometers.kicad_sch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]
2024-12-06 Changes for new steering position system
    [PUTM_EV_Frontbox_2023.kicad_pcb, PUTM_EV_Frontbox_2023.kicad_sch, Steering_Position_2.kicad_sch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]
2024-12-06 Changes in power section
    [PUTM_EV_Frontbox_2023.kicad_pcb, PUTM_EV_Frontbox_2023.kicad_sch, Steering_Position_2.kicad_sch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]
2024-12-08 Frontbox 2025 Version 1.0
    [PUTM_EV_Frontbox_2023.kicad_pcb, PUTM_EV_Frontbox_2023.kicad_sch, Tensometers.kicad_sch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]
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2024-12-10 Added 3D models of tensometers connectors
    [PUTM_EV_Frontbox_2023.kicad_pcb]
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2025-03-06 Change voltage followers for tensometer to non iverting ampifiers
    [PUTM_EV_Frontbox_2023.kicad_pcb, Tensometers.kicad_sch]
2025-03-07 Changes in conventer layout
    [PUTM_EV_Frontbox_2023.kicad_pcb]
2025-03-08 Created hardware version 1.1.0
    [PUTM_EV_Frontbox_2023.kicad_pcb]
2025-03-11 Changes in converter layout and tensometers schematic
    [PUTM_EV_Frontbox_2023.kicad_pcb, PUTM_EV_Frontbox_2023.kicad_sch, Tensometers.kicad_sch]
2025-03-12 Changes Vcc op-amps in brakes pressure (3V3 to 5V) and mcp6002 footprint (to MSOP8)
    [PUTM_EV_Frontbox_2023.kicad_pcb, Steering_Position_2.kicad_sch, Tensometers.kicad_sch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]
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

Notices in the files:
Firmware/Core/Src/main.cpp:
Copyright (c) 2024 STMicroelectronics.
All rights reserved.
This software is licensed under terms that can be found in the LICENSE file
